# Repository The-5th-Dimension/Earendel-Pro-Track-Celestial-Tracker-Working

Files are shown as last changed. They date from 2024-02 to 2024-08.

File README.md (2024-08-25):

<h1>Earendel Pro-Track: IoT-Based Celestial Object Tracker</h1>

<h2><a href="https://github.com/linukaratnayake">Linuka Ratnayake</a>, <a href="https://github.com/YasiruDEX">Yasiru Basnayake</a>, <a href="https://github.com/KumuthuDeZoysa">Kumuthu De Zoysa</a>, <a href="https://github.com/KavinduJ2001">Kavindu Jayathissa</a>, <a href="https://github.com/ehele">Aruna Ehelepola</a>,  <a href="">Dhanushka Weerakoon</a></h2>

<h2>Overview</h2>
<h3>Introduction</h3>
<p>
    "Earendel Pro-Track" is a project that aims to design a telescope mount capable of automatically locating and keeping track of stellar objects. The desired stellar object can be selected through the user interface, and once that information is transferred to the telescope mount in the form of celestial coordinates, it turns to that stellar object, and starts observing.
</p>

<h3>Features</h3>
<ul>
    <li>No need to horizontally level the telescope mount.</li>
    <li>No need to start by pointing to the direction of North or the North Star.
    <li>Integration with online databases to obtain real-time celestial locations.</li>
    <li>Mobile app interface for easy controlling for the user.</li>
    <li>IoT communication for transmitting mount orientation data.</li>
    <li>Carefully designed for smooth and accurate celestial tracking.</li>
</ul>

https://github.com/user-attachments/assets/d0daafc0-86b6-4ca8-b112-ab7fa79acf01

To better understand the project and its problem-solution scenario, deliverables and outcomes, refer to <a href="Project Details (Documents and Media)/Project Overview Video/Earendel_Pro_Track _The_5th_Dimension.mp4">this</a> video.

<h2>Research and Development</h2>

<h3>Coordinate Systems and Conversion</h3>

| **Altitude - Azimuth** | **Right Ascension - Declination** |
|:--:|:--:|
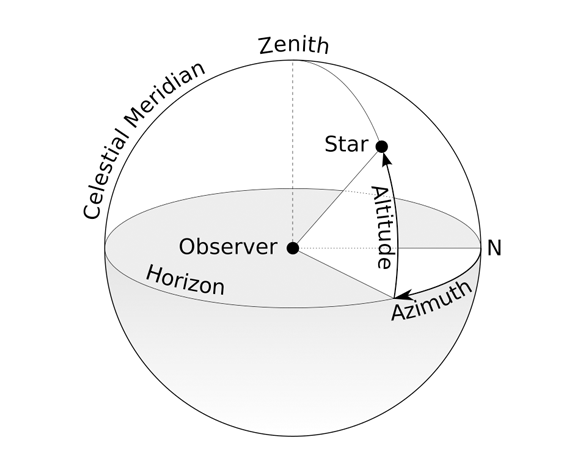
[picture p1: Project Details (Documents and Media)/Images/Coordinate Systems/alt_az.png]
ALT-AZ
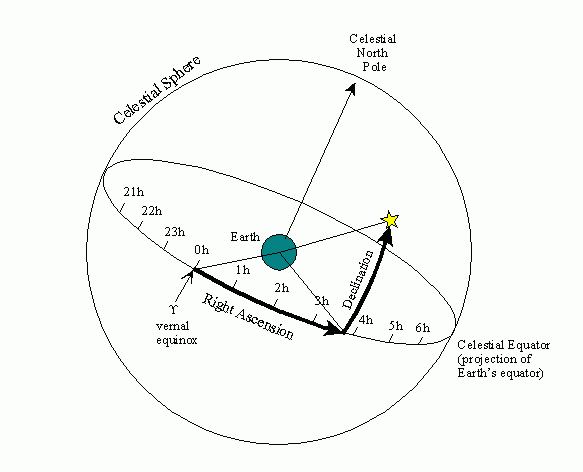
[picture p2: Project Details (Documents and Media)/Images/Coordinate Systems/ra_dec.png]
|  | |

These are two main coordinates systems used in astronomy.
Coordinates given in the latter are relatively constant and can be obtained from databases. They then need to be converted to the former, taking into consideration the user's location and the date and time.

The location and date and time are acquired from the sensors and the internet, and converted with the custom-written libraries.

<b>In this project, the conversion from Right Ascension and Declination coordinates to Altitude and Azimuth coordinates was improved by accounting for the tilt of the telescope mount. For further details, please refer to the following personal repository.

<a href="https://github.com/linukaratnayake/RADEC-to-ALTAZ-Tilted-Axes-Coordinate-Conversion">linukaratnayake/RADEC-to-ALTAZ-Tilted-Axes-Coordinate-Conversion</a></b>

**Repository Content**

<ul>
<li>Algorithm to convert Right Ascension and Declination coordinates to Altitude and Azimuth coordinates.</li>
<li>Mathematical derivation of an algorithm to compensate for the tilt in the coordinate axes.</li>
<li>Python implementation of the algorithms for testing and as a proof of concept.</li>
<li>C/C++ implementation of the algorithms to be used in the actual device.</li>
</ul>

<h2>Software Development</h2>

In the project, it was aimed to provide the flexibility to the user such that it is possible to use a mobile device or a computer to control the telescope mount. This includes developing a mobile application (currently Android, plan to extend to iOS), and a web interface, through which the user can select the desired stellar object.

Furthermore, software development includes designing of databases to store data of stars and planets, as well as handling user details.

<h3>Mobile App</h3>

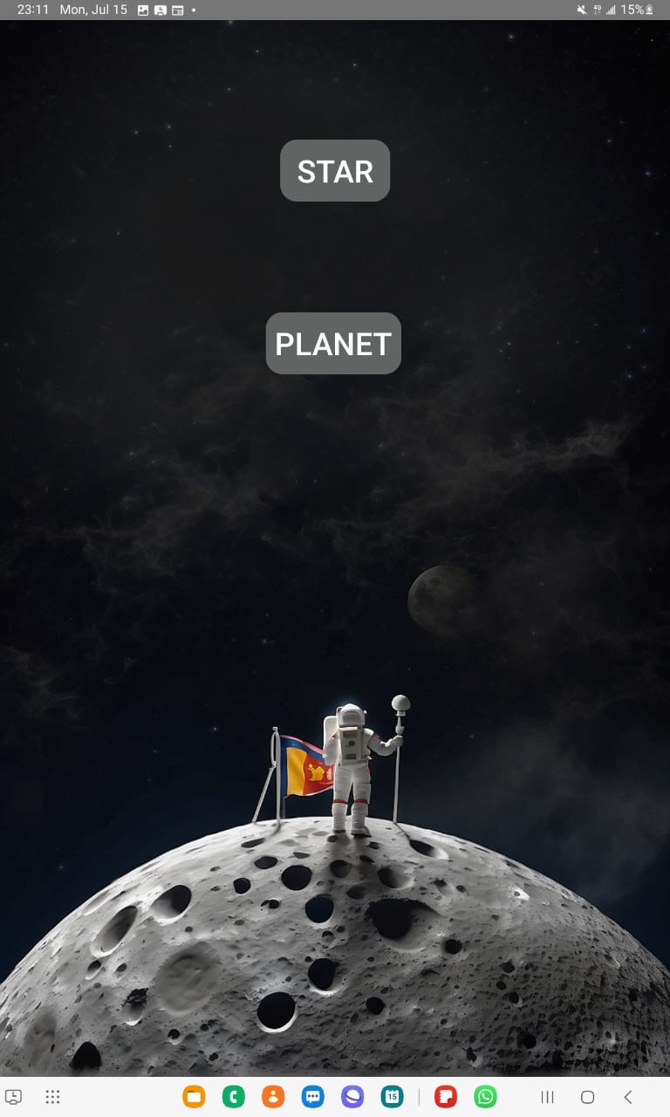
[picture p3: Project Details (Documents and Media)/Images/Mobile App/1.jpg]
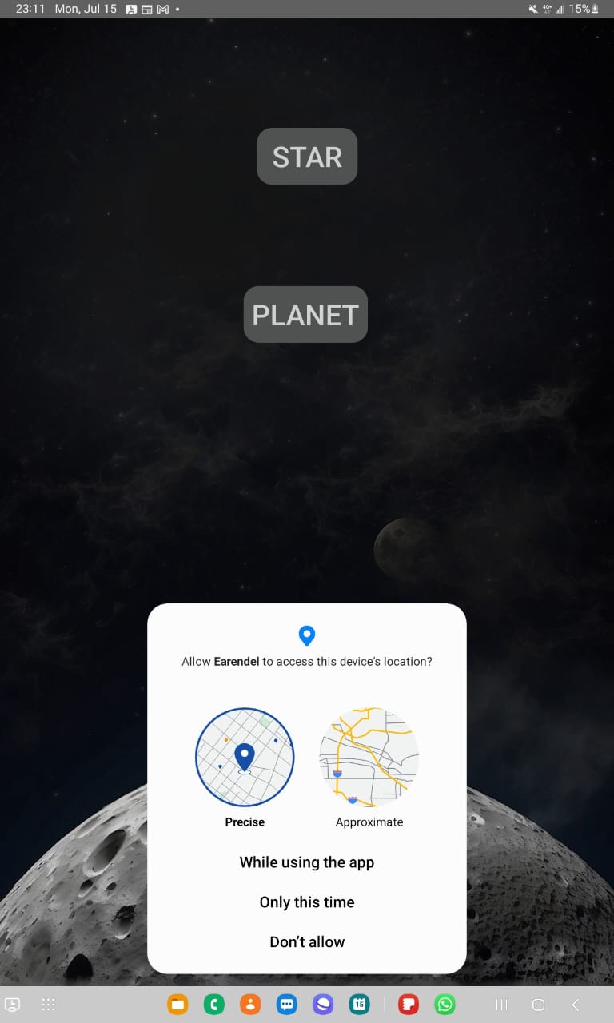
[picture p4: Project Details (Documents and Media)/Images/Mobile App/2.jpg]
|  | |
|:--:|:--:|
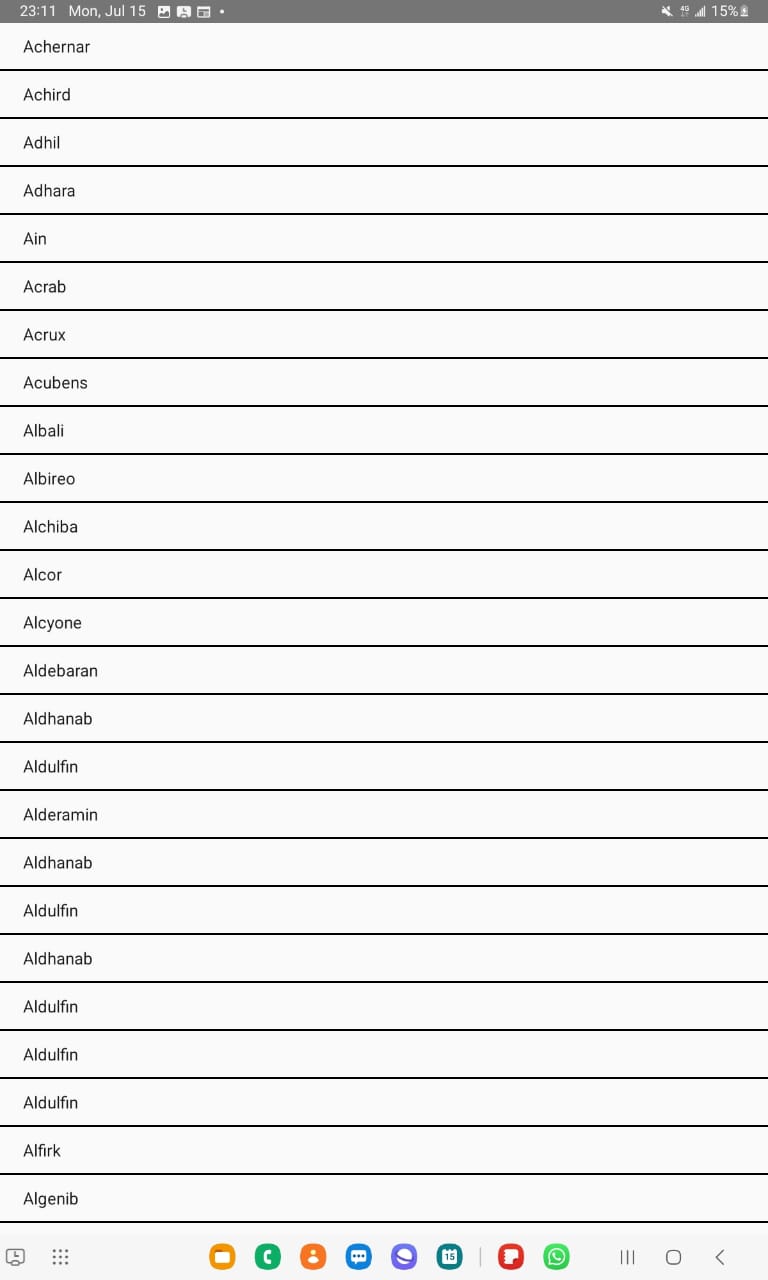
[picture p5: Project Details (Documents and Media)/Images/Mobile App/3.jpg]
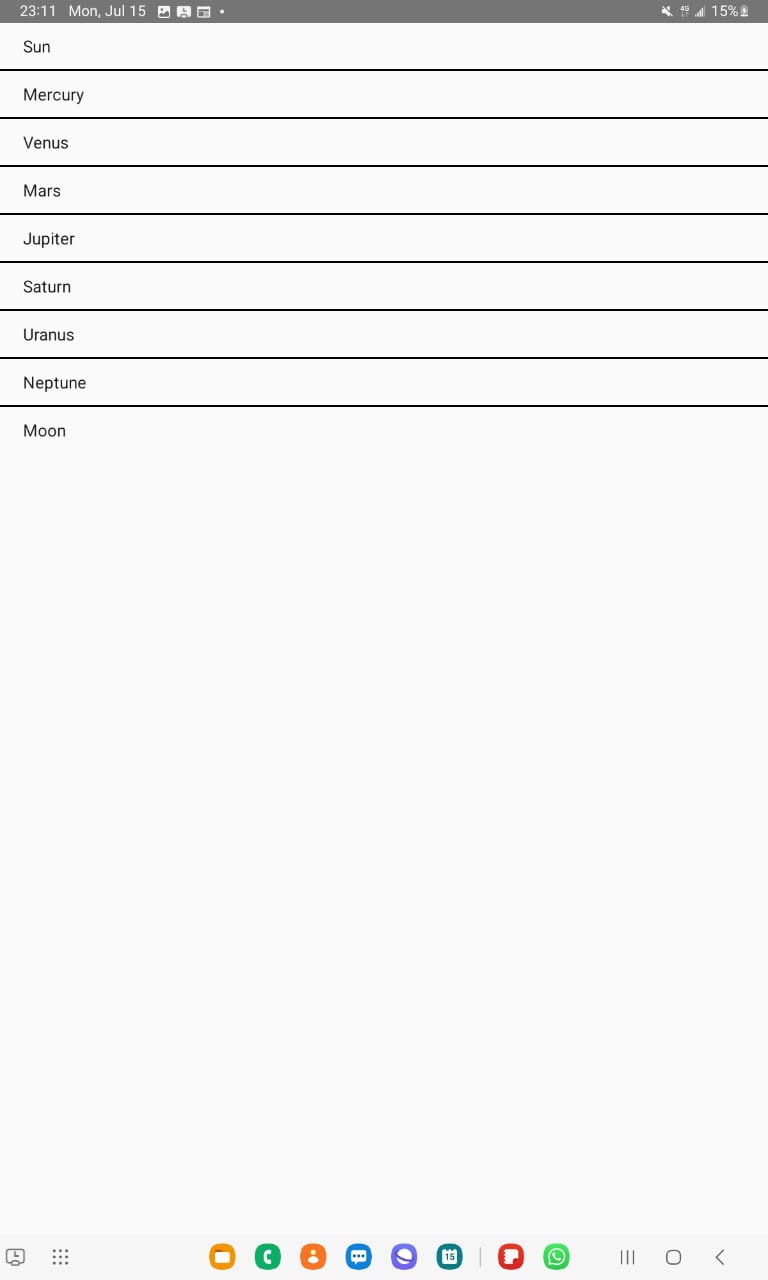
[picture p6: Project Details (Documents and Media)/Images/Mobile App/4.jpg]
|  | |

<h3>Web Application</h3>

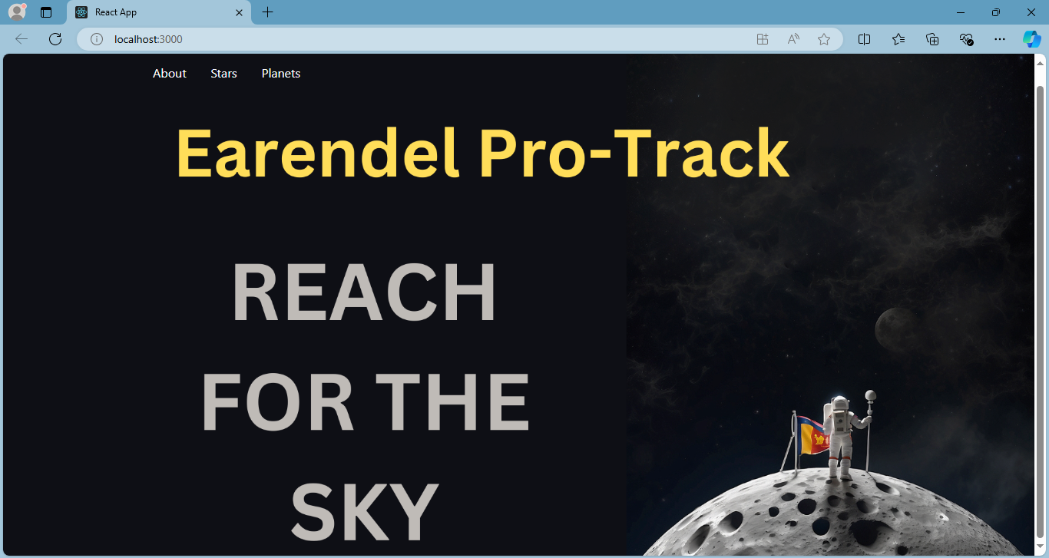
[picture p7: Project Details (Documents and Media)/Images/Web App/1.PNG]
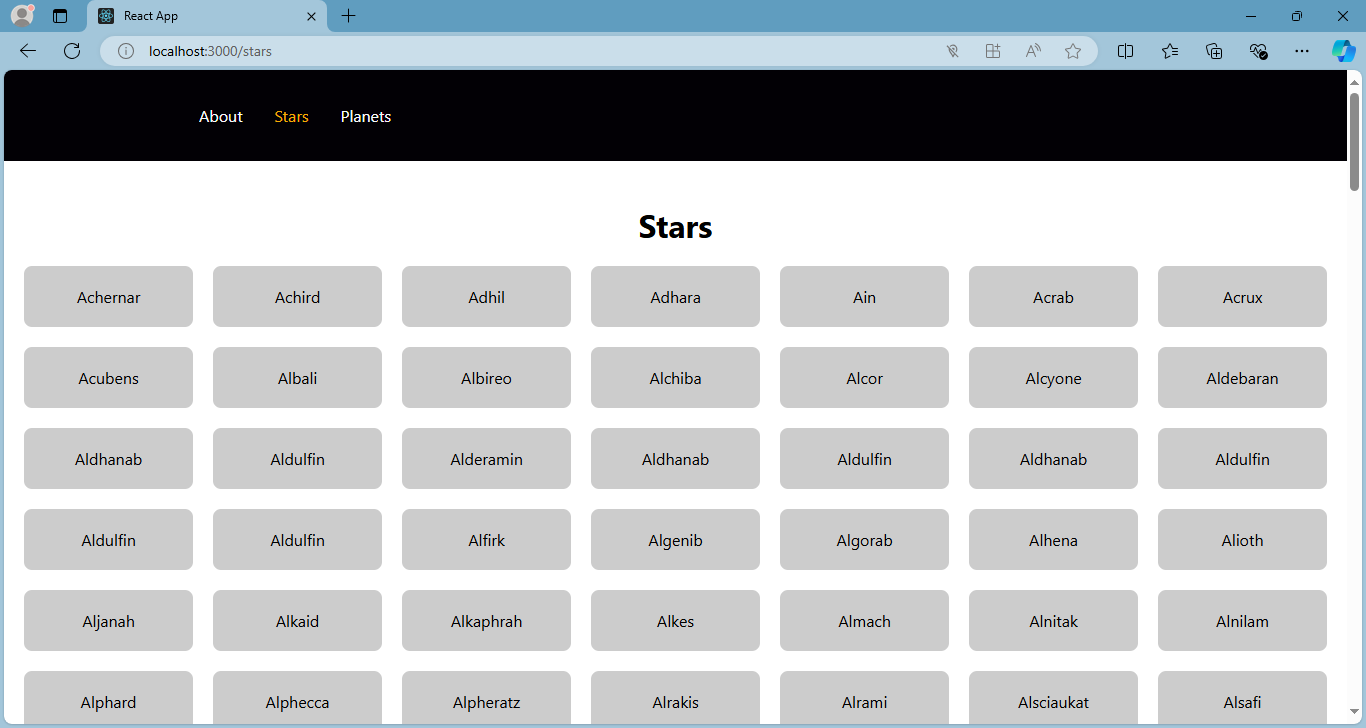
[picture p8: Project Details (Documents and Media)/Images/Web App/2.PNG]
|  | |
|:--:|:--:|
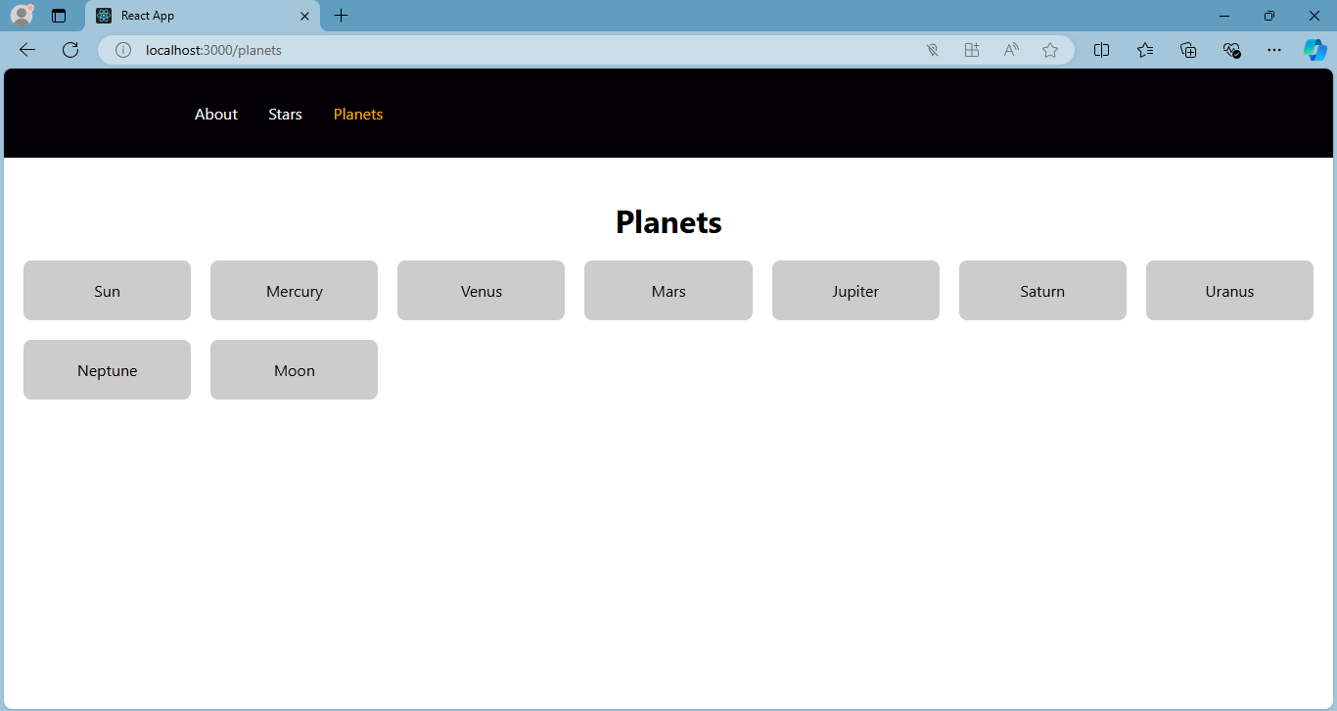
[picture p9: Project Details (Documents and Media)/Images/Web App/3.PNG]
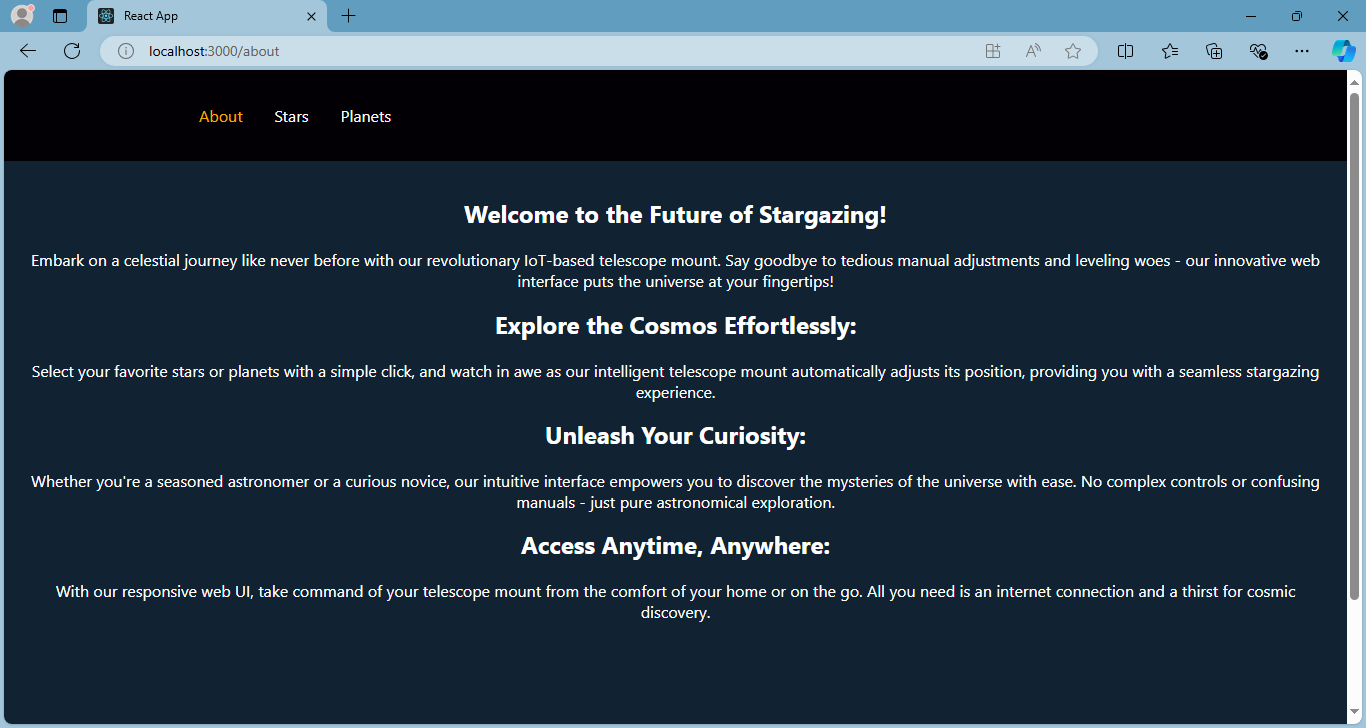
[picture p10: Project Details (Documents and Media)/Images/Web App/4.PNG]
|  | |

For codes and further details of the user application and the inclusion of databases, refer <a href="Codes/User Application/">here</a>.

<h2>PCB Design</h2>

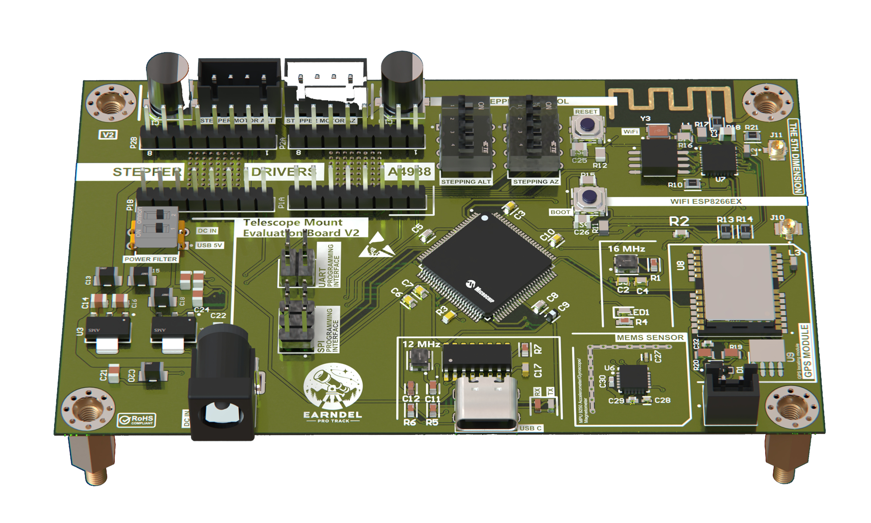
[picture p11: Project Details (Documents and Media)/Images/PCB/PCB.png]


A custom 2-layer PCB is designed using **Altium Designer**.

**Features of the PCB**
<ul>
<li>Division of synchronous and asynchronous processing parts between two microcontrollers, to reduce latency, and seamless and smoother movements.</li>
<li>2 power-up methods: DC barrel jack up to 12V, and USB type C port.</li>
<li>Compact design with on-board mounted stepper motor drivers, and control switches.</li>
<li>External connection ports for integrating accelerometer, magnetometer, and GPS module.</li>
</ul>

For PCB design files, refer <a href="PCB Design">here</a>.

<!-- <b>In the second version of the PCB, several identified issues were resolved, together with the addition of some more features. For further details, please refer to the following personal repository.

<a href="https://github.com/YasiruDEX?tab=repositories">[repo_name]</a></b> -->

<h2>Mechanical Design</h2>

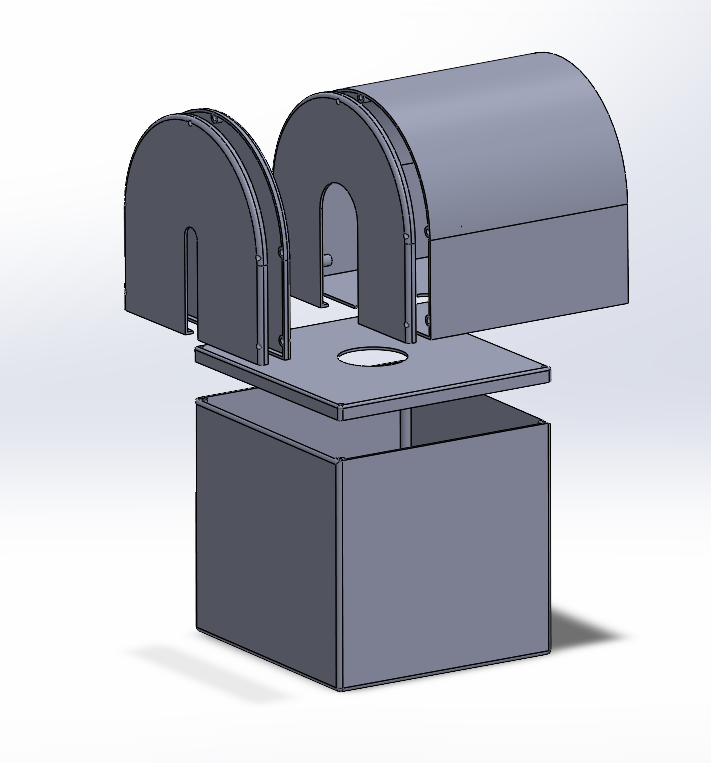
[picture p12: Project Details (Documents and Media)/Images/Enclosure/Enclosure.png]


Metal structure is designed to support the weight of the telescope, motors, and other components, with a 3D printed enclosure to enhance the visual appeal. **SOLIDWORKS** and **Blender** are used extensively for designing.

For structure and enclosure design files, and details, refer <a href="Physical Design">here</a>.

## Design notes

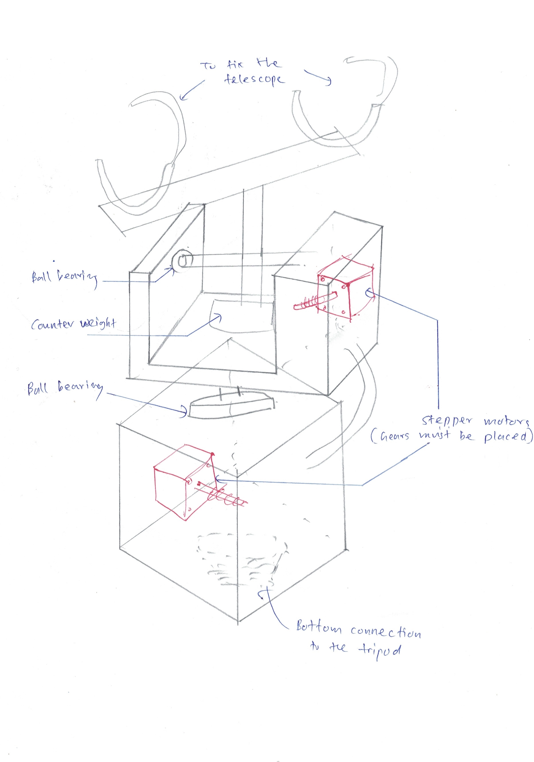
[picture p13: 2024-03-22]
Physical Design/Mount - Hand Drawn Sketches/Hand_Drawn_Sketch_1.jpg

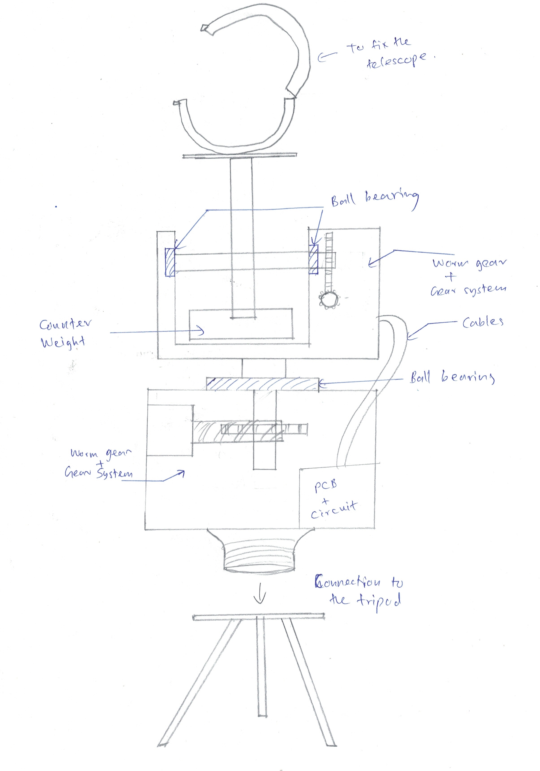
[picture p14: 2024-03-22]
Physical Design/Mount - Hand Drawn Sketches/Hand_Drawn_Sketch_2.jpg

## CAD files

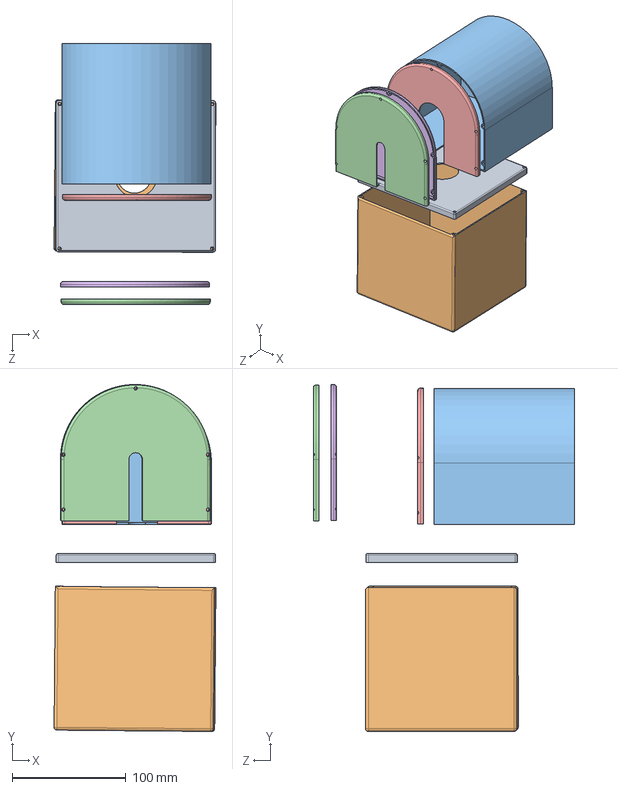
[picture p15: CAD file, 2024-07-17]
Physical Design/Enclosure Design/Assembly.SLDASM
142.2 x 304.8 x 229.7 mm
Bottom Box Lid Part
Bottom Box Part
Top Cover With Arch Part 1
Top Cover With Arch Part 2
Thin Cover Part 1
Thin Cover Part 2

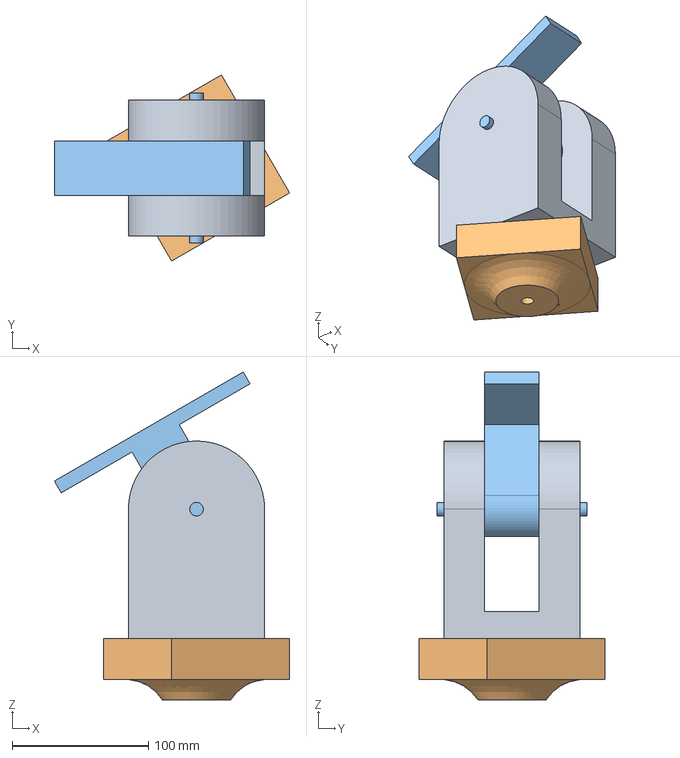
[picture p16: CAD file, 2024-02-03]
Physical Design/Mount - Initial Designs/mount.step
172.6 x 136.6 x 240.6 mm

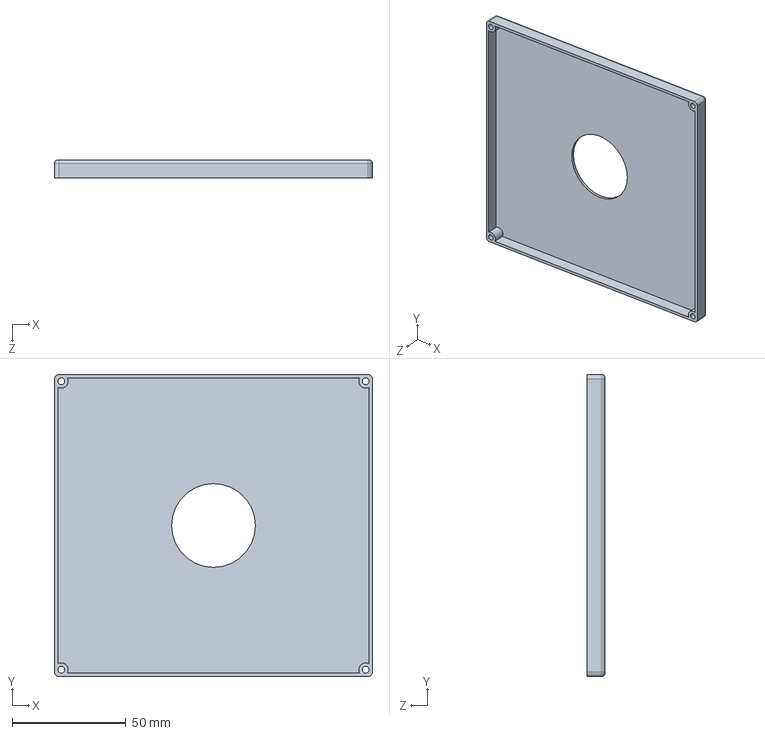
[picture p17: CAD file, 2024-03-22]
Physical Design/Enclosure Design/Bottom Box Lid Part.SLDPRT
140.0 x 133.0 x 8.00 mm

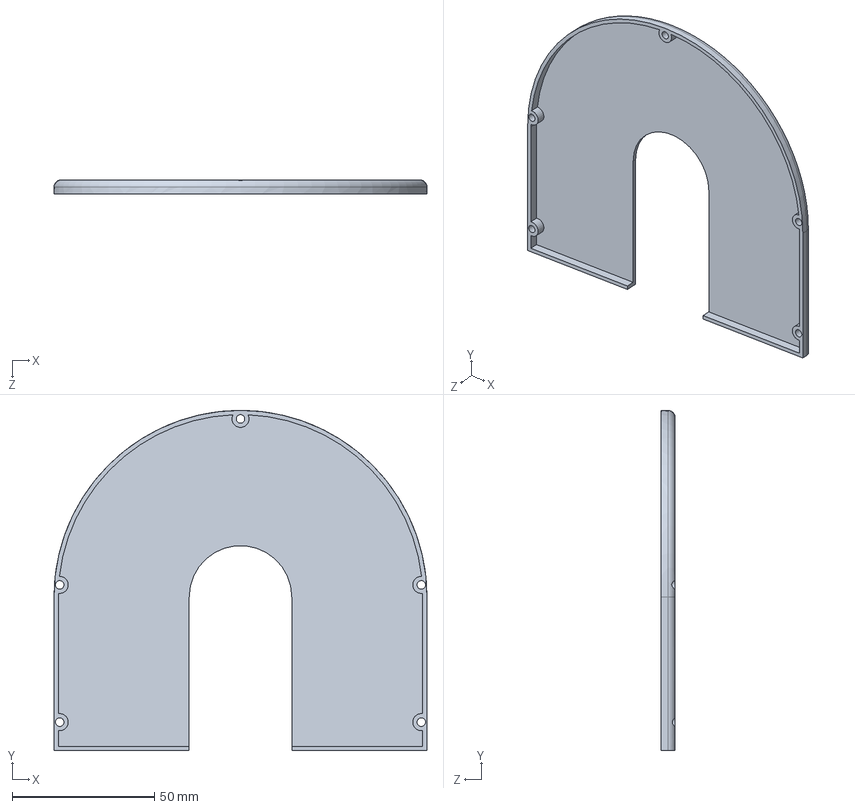
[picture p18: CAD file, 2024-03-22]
Physical Design/Enclosure Design/Thin Cover Part 1.SLDPRT
131.0 x 119.5 x 5.00 mm

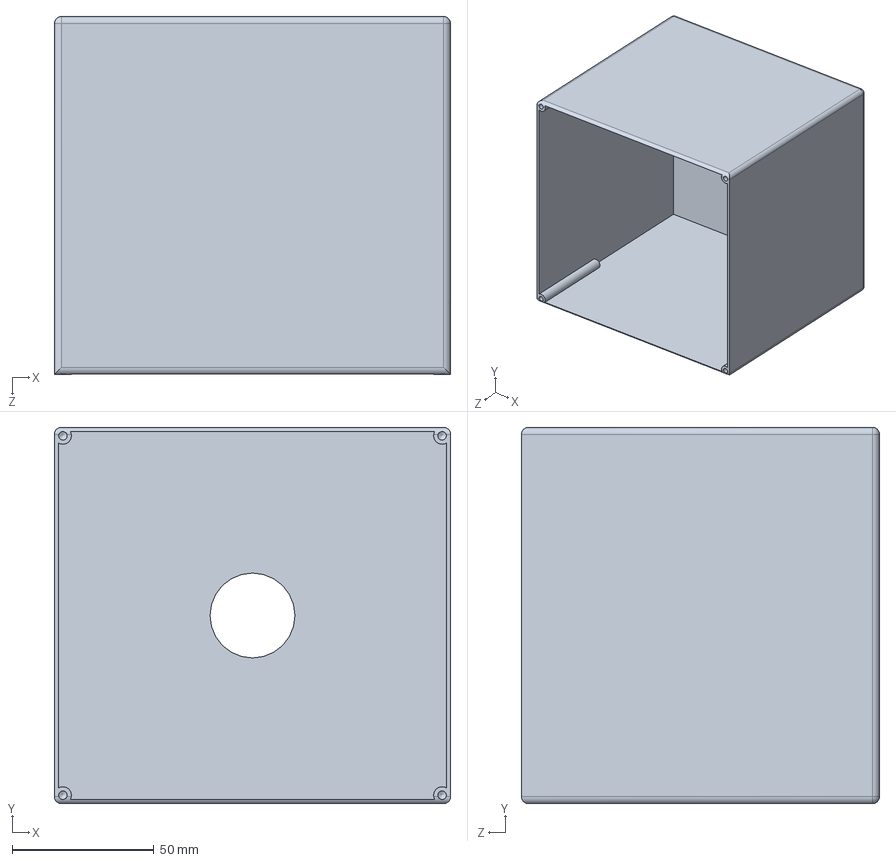
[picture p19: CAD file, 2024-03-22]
Physical Design/Enclosure Design/Bottom Box Part.SLDPRT
140.0 x 133.0 x 126.5 mm

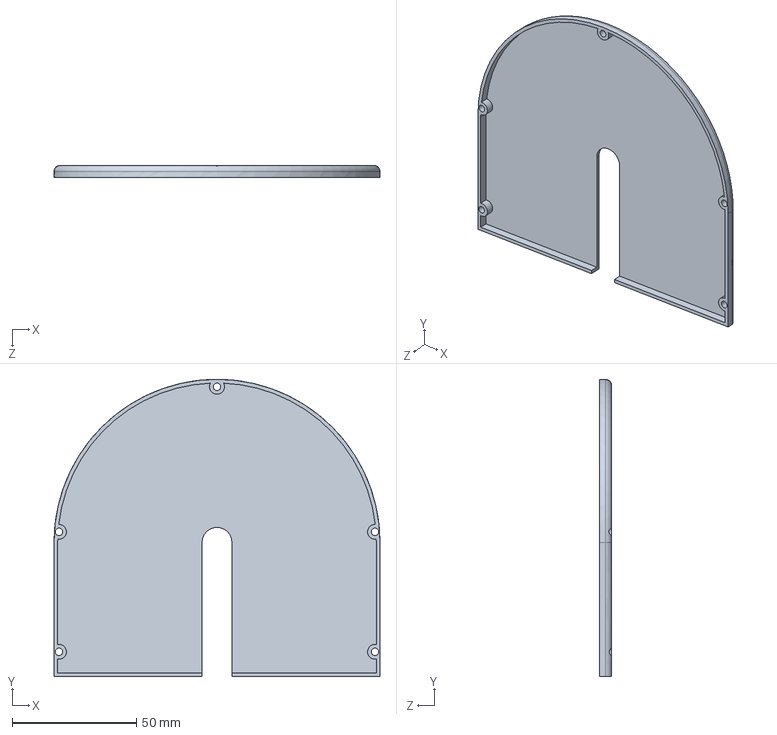
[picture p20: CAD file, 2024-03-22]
Physical Design/Enclosure Design/Top Cover With Arch Part 2.SLDPRT
131.0 x 119.5 x 5.00 mm

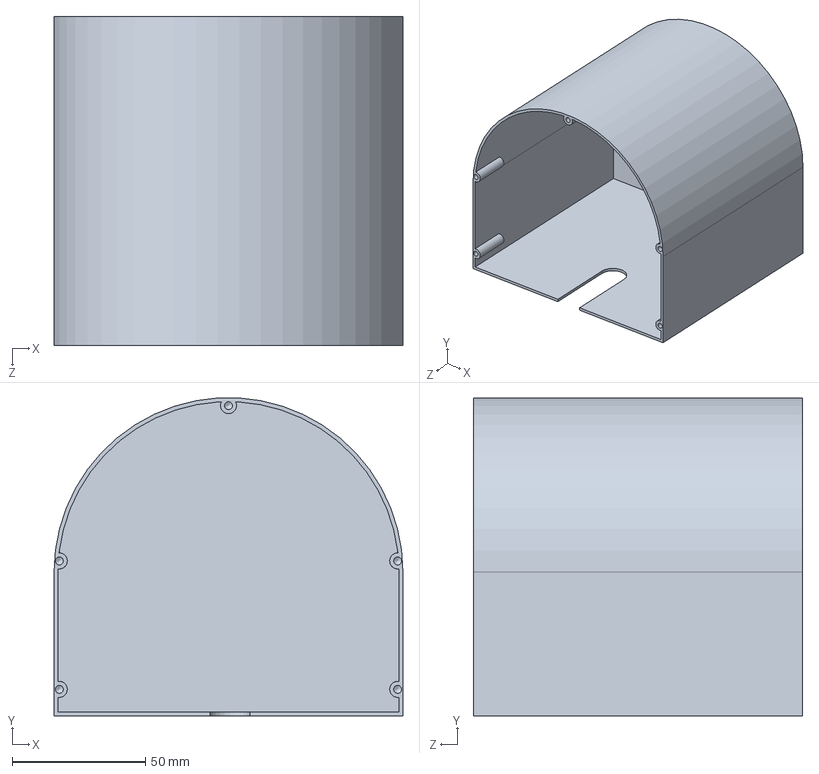
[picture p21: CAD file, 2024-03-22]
Physical Design/Enclosure Design/Top Cover With Arch Part 1.SLDPRT
131.0 x 119.4 x 123.5 mm

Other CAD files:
Physical Design/Enclosure Design/Thin Cover Part 2.SLDPRT
Physical Design/GearBox_design/V1.blend
Physical Design/GearBox_design/v2.blend
Physical Design/Mount - Initial Designs/mount.SLDPRT
Physical Design/Mount - Initial Designs/mount.dwg

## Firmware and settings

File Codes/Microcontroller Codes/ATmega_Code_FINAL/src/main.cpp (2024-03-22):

/*

PROJECT PLAN

1. Use external interrrupts to trigger a UART transfer from the ESP32.
2. Get serial data about GPS location, UTC time, and RA-DEC coordinates.
3. Use the already built library to convert RA-DEC to ALT-AZ.
4. Turn the stepper motors to the required stellar object.
5. Keep focusing until another interrupt gives another object.
(Time updates can also come from an interrupt.)

*/

#include <Arduino.h>
#include <StandardCplusplus.h>
#include <vector>
#include "CoordinateConverter.h"
#include "DataDecoder.h"
#include "Stepper.h"
#include "Accelerometer.h"
#include "PseudoMagnetometer.h"

// The accelerometer we use is an MPU6050.
#define ACC_I2C_ADDR 0x68

#define AZIMUTH_ANGULAR_RESOLUTION 5 // degrees
#define ALTITUDE_ANGULAR_RESOLUTION 5 // degrees

// #define Serial_INT 2 // Interrupts seem not working.

// Variables to be updated based on the Serial data from the ESP32.

// SOME RANDOM (EXPECTED ON DEMONSTRATION DAY) VALUES ARE SET FOR BETTER ACCURACY.
volatile int year = 2024, month = 3, day = 23, hour = 4, minute = 30; // Expected day and time of demonstration.
volatile double second = 0;
volatile double latitude = 6.9271, longitude = 79.8612;
double ra = 6.75, dec = -16.7;  // Sirius
bool valuesUpdated = true;
double currentAzimuth = 0;
unsigned int azimuthStep = 0;

// Local coordinate values.
double altitude = 0, azimuth = 0;

float roll = 0;
// float yawn = 0;

CoordinateConverter converter;
Accelerometer accelerometer;

// Function Declarations
void handleSerial();
void autoUpdateTime();
void debugPrint();
double absolute(double); // Custom function to find the absolute value.

void setup()
{
  // Serial output for debug data output.
  Serial.begin(115200);

  accelerometer.begin(ACC_I2C_ADDR);

  // Need the accelerometer to be horizontally flat.
  // If not practical, comment this out.
  // accelerometer.calibrateError();
  
  pinModeSteppers();

  // Maybe need to add some initial delay to get the initial data from the ESP32 in the setup.

  autoUpdateTime(); 
}

void loop()
{
  handleSerial();

  if (valuesUpdated)
  {
    converter.updateLocation(latitude, longitude);
    converter.updateDateUTC(day, month, year);
    converter.updateTimeUTC(hour, minute, second);
    converter.update_RA_DEC(ra, dec);
    valuesUpdated = false;
  }

  converter.updateTimeUTC(hour, minute, second);
  converter.updateDateUTC(day, month, year); // Only necessary on a moment after midnight.

  vector<double> altaz = converter.convert();
  altitude = altaz[0];
  azimuth = altaz[1];

  // Lowest angle for the telescope is 0 degrees.
  if (altitude < 0) {
    altitude = 0;
  }

  // Turn bottom part to `azimuth`.

  // ===== WORKS ONLY WITH A MAGNETOMETER =====
  // yawn = 0; // Magnetometer.getYawn();  // This should return absolute angle from the North.
  // bool motorDirectionDown = (azimuth - yawn) >= 0;  // Might neeed to change to <=, depending on the actual setup.
  // if (absolute(azimuth - yawn) > AZIMUTH_ANGULAR_RESOLUTION) {
  //   rotate(STEPPER_DOWN, motorDirectionDown);
  // }
  // ==========


  // ALTERNATE METHOD WITHOUT A MAGNETOMETER
  // THIS METHOD REQUIRES THE INITIAL ALIGNMENT TO NORTH.
  //========================
  bool motorDirectionDown;
  // Might need to interchange >= and <, depending on the actual setup.
  if (currentAzimuth >= azimuth) {
    motorDirectionDown = DIR_1;
  }
  else if (currentAzimuth < azimuth) {
    motorDirectionDown = DIR_2;
  }

  double remainingAngle = absolute(currentAzimuth - azimuth);


  if ((azimuthStep < angleToSteps(remainingAngle)) &&  (absolute(currentAzimuth - azimuth) > AZIMUTH_ANGULAR_RESOLUTION)) {
    rotate(STEPPER_DOWN, motorDirectionDown);
    if (currentAzimuth >= azimuth) {
      currentAzimuth -= stepsToAngle(1);
    }
    else if (currentAzimuth < azimuth) {
      currentAzimuth += stepsToAngle(1);
    }
    azimuthStep++;
  }

  // Turn top part to `altitude`.
  roll = accelerometer.getRoll(); // Either roll or pitch depending on how the accelerometer is mounted.
  bool motorDirectionUp = altitude >= roll;  // Might neeed to change to <=, depending on the actual setup.
  if (absolute(altitude - roll) > ALTITUDE_ANGULAR_RESOLUTION) {
    rotate(STEPPER_UP, motorDirectionUp);
  }

  // // DEBUG
  // debugPrint();
}

// Function Definitions
void handleSerial()
{
  if (Serial.available())
  {
    const int buffSize = 50;
    char input[buffSize];
    Serial.readStringUntil('\n').toCharArray(input, buffSize);

    data inputData = decode(input);

    if (inputData.type == "DATE")
    {
      day = (int)inputData.value1;
      month = (int)inputData.value2;
      year = (int)inputData.value3;
    }
    else if (inputData.type == "TIME")
    {
      hour = (int)inputData.value1;
      minute = (int)inputData.value2;
      second = inputData.value3;
    }
    else if (inputData.type == "GPS")
    {
      latitude = inputData.value1;
      longitude = inputData.value2;
    }
    else if (inputData.type == "RADEC")
    {
      ra = inputData.value1;
      dec = inputData.value2;
    }

    valuesUpdated = true;
  }

  // == TODO ==
  // Send an acknowledgement back to the ESP32 after a successful reception of data.
}

void autoUpdateTime()
{
  // The following are internal registers in ATmega328.
  // Internal interrupts (Timers) are used to keep track of time precisely.
  TCCR1A = 0;
  TCCR1B = 0;
  TCNT1 = 3036;
  TCCR1B |= (1 << CS12);
  TIMSK1 |= (1 << TOIE1);
}

ISR(TIMER1_OVF_vect)
{
  second += 1;
  if (second >= 60)
  {
    second = 0;
    minute += 1;
  }
  if (minute >= 60)
  {
    minute = 0;
    hour += 1;
  }
  if (hour >= 24)
  {
    hour = 0;
    day += 1;
  }
  // This should be extended to work well with month and year boundaries.
  // e.g.: Update from 30th June to 1st of July.
  // However, let's assume this is enough for demonstration.

  // Setting back to 3036, otherwise it starts back from 0.
  TCNT1 = 3036;
}

void debugPrint() {
  Serial.print(String(year) + "." + String(month) + "." + String(day) + "\t");
  Serial.print(String(hour) + ":" + String(minute) + "." + String(second) + "\t");
  Serial.print("Latitude: " + String(latitude) + ", Longitude: " + String(longitude) + "\t");
  Serial.print("RA: " + String(ra) + ", DEC: " + String(dec) + "\t");
  Serial.print("Altitude: " + String(altitude) + ", Azimuth: " + String(azimuth) + "\t");
  // Serial.print("Roll: " + String(roll) + ", Yawn: " + String(yawn) + "\t");
  Serial.print("Roll: " + String(roll) + ", CurrentAzimuth: " + String(currentAzimuth) + "\t");
  Serial.println();
}

double absolute(double value) {
  if (value >=0 ) {
    return value;
  }
  else {
    return -1 * value;
  }
}

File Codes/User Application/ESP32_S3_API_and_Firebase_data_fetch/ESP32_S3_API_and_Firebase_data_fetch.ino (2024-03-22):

#include <Arduino.h>
#include "WiFiManager.h"
#include "FirebaseManager.h"
#include "HTTPManager.h"
#include "LCDManager.h"
#include <time.h>

LiquidCrystal_I2C lcd(0x27, 20, 4);

#define _SSID "Dialog 4G 752"         // Your WiFi SSID
#define _PASSWORD "b10F79cD"     // Your WiFi Password
// #define _SSID "Yasiru's Galaxy Tab"          // Your WiFi SSID
// #define _PASSWORD "unlimited"      // Your WiFi PasswordString serverPath = serverName;
const char* referenceUrl = "earendeldata-default-rtdb.asia-southeast1.firebasedatabase.app";
const char* httpUrl = "https://api.visibleplanets.dev/v3?latitude=7.4818&longitude=80.3609&showCoords=true&aboveHorizon=false";
const char* FirebaseUrl = "https://earendeldata-default-rtdb.asia-southeast1.firebasedatabase.app/";

const char* ntpServer = "pool.ntp.org";
const long  gmtOffset_sec = 0; // Timezone offset in seconds (e.g. 0 for GMT)
const int   daylightOffset_sec = 3600; // Daylight offset in seconds (e.g. 3600 for DST)

#define az "Z"
#define alt "Y"

FirebaseManager firebase(referenceUrl);
WiFiManager wifiManager(_SSID, _PASSWORD, lcd);
HTTPManager httpManager;
// FirebaseManagerNew httpManager;

const int MAX_PLANETS = 10;
const int numberOfPlanets = 10;

float az_current_angle = 0;
float alt_current_angle = 0;
float az_to_turn = 0;
float alt_to_turn = 0;

String planetNames[MAX_PLANETS];
String raValues[MAX_PLANETS];
String decValues[MAX_PLANETS];

const String planetsWithMoon[numberOfPlanets] = {
  "Sun", "Moon", "Mercury", "Venus", "Mars", "Jupiter", "Saturn", "Uranus", "Neptune"
};

String planetNeeded;
String starData;
String prevPlanet;

int now_time;

// Function declarations
int findIndex(const String array[], int size, const String &targetValue);
void initialize();
void handlePlanetData();
void handleStarData();

void setup() {
  lcd.init();
  lcd.backlight();
  Serial.begin(115200);
  // pinMode(LED_BUILTIN, OUTPUT);
  // digitalWrite(LED_BUILTIN, LOW);
  WiFi.mode(WIFI_STA);
  WiFi.disconnect();
  delay(1000);

  // Connect to WiFi
  Serial.println();
  Serial.println();
  Serial.print("Connecting to: ");
  Serial.println(_SSID);
  WiFi.begin(_SSID, _PASSWORD);

  while (WiFi.status() != WL_CONNECTED) {
    delay(500);
    Serial.print("-");
  }

  Serial.println("");
  Serial.println("WiFi Connected");

  // Print the IP address
  Serial.print("IP Address: ");
  Serial.print("http://");
  Serial.print(WiFi.localIP());
  Serial.println("/");
  // digitalWrite(LED_BUILTIN, HIGH);

//================================================================//
//================================================================//


  Serial.println();
  Serial.println();
  Serial.println();
  // initialize();
  now_time = -30;

  // Initialize and synchronize the time
  configTime(gmtOffset_sec, daylightOffset_sec, ntpServer);

  // Wait for time to be set
  while (!time(nullptr)) {
    delay(1000);
    Serial.println("Waiting for time to sync...");
  }

}

void loop() {

  // Get current time
  time_t now;
  struct tm timeinfo;
  char strftime_buf[64];

  time(&now);
  localtime_r(&now, &timeinfo);
  
  // Format time into a string
  strftime(strftime_buf, sizeof(strftime_buf), "%Y-%m-%d %H:%M:%S", &timeinfo);
  
  // Print time to serial
  Serial.print("Current time: ");
  Serial.println(strftime_buf);

  if (millis()/1000 - now_time >= 10){
    planetNeeded = firebase.getString("Planet");
    // planetNeeded = "Sun";

    Serial.println(planetNeeded);
    
    bool planetFound = findIndex(planetsWithMoon, numberOfPlanets, planetNeeded) != -1;
    
    if (planetFound) {
      handlePlanetData();
    } else {
      handleStarData();
    }

    prevPlanet = planetNeeded;
    Serial.println();
    now_time = millis()/1000;
  }

    if(int(az_to_turn) != int(az_current_angle)){
      if (az_to_turn > az_current_angle){
      Step(az, 1, true);
      az_current_angle += 1.8;
      // delay(50);
      }else if (az_to_turn < az_current_angle){
      Step(az, 1, false);
      az_current_angle -= 1.8;
      // delay(50);
      }
    }

    if(int(alt_to_turn) != int(alt_current_angle)){
      if (alt_to_turn > alt_current_angle){
      Step(alt, 1, true);
      alt_current_angle += 1.8;
      // delay(50);
      }else if (alt_to_turn < alt_current_angle){
      Step(alt, 1, false);
      alt_current_angle -= 1.8;
      // delay(50);
      }
    }

    // zAxisServo.write(az_current_angle);
    // Serial.print(alt_to_turn);
    // Serial.print(" : ");
    // Serial.print(alt_current_angle);
    // Serial.print(" : ");
    // Serial.print(az_to_turn);
    // Serial.print(" : ");
    // Serial.println(az_current_angle);
}

// Function definitions
void initialize() {
  wifiManager.connect();
}

void handlePlanetData() {
  Serial.print("Finding Planet Data");
  httpManager.fetchData(httpUrl, planetNames, raValues, decValues);

  int index = findIndex(planetNames, MAX_PLANETS, planetNeeded);

  if (index != -1) {
    int degreeIndex = raValues[index].indexOf('h');
    int altdegreeIndex = decValues[index].indexOf("°");
    Serial.print(decValues[index]);
    Serial.println(planetNeeded + " : RA: " + raValues[index] + " : DEC:" + decValues[index]);

    az_to_turn = int(atoi(raValues[index].substring(0, degreeIndex).c_str())/1.8) * 7 * 1.8 * 2;

    alt_to_turn = -abs(int(atoi(decValues[index].substring(0, altdegreeIndex).c_str())/1.8))  * 1.8;

    if(az_to_turn >= 360){az_to_turn -= 360;}

    lcd.setCursor(0, 1);
    lcd.print("              ");
    lcd.setCursor(0, 1);
    lcd.print(planetNeeded + ":");
    lcd.setCursor(0, 2);
    lcd.print("RA: " + String(raValues[index]));
    lcd.setCursor(0, 3);
    lcd.print("DEC: " + String(decValues[index]));
  } else {
    Serial.println("Planet not found!");
  }
}

void handleStarData() {
  if (planetNeeded != prevPlanet) {
    starData = firebase.getString(planetNeeded);
  }

  az_to_turn = int(atoi(starData.substring(3, 10).c_str())/1.8) * 7 * 1.8 * 2;

  alt_to_turn = -abs(int(atoi(starData.substring(15, 24).c_str())/1.8))  * 1.8;

  if(az_to_turn >= 360){az_to_turn -= 360;}


  Serial.println(planetNeeded + ": " + starData);
  lcd.setCursor(0, 1);
  lcd.print("              ");
  lcd.setCursor(0, 1);
  lcd.print(planetNeeded + ":");
  lcd.setCursor(0, 2);
  lcd.print(starData.substring(0, 10));
  lcd.setCursor(0, 3);
  lcd.print(starData.substring(11, 24));
}

int findIndex(const String array[], int size, const String &targetValue) {
  for (int i = 0; i < size; i++) {
    if (array[i] == targetValue) {
      return i;
    }
  }
  return -1;
}
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

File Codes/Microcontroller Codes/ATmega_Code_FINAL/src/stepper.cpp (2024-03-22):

#include <Arduino.h>
#include "Stepper.h"

void pinModeSteppers() {
    pinMode(STEPPER_DOWN_STEP, OUTPUT);
    pinMode(STEPPER_DOWN_DIR, OUTPUT);

    pinMode(STEPPER_UP_STEP, OUTPUT);
    pinMode(STEPPER_UP_DIR, OUTPUT);
}

void rotate(int motor, int direction) {
    if (motor == STEPPER_DOWN) {
        if (direction == DIR_1) {
            digitalWrite(STEPPER_DOWN_DIR, LOW);
        }
        else if (direction == DIR_2) {
            digitalWrite(STEPPER_DOWN_DIR, HIGH);
        }

        digitalWrite(STEPPER_DOWN_STEP, HIGH); 
        delayMicroseconds(500);
        // delay(30);
        digitalWrite(STEPPER_DOWN_STEP, LOW); 
        delayMicroseconds(500);
        // delay(30);
    } else if (motor == STEPPER_UP) {
        if (direction == DIR_1) {
            digitalWrite(STEPPER_UP_DIR, LOW);
        }
        else if (direction == DIR_2) {
            digitalWrite(STEPPER_UP_DIR, HIGH);
        }

        digitalWrite(STEPPER_UP_STEP, HIGH); 
        delayMicroseconds(500);
        // delay(30);
        digitalWrite(STEPPER_UP_STEP, LOW); 
        delayMicroseconds(500);
        // delay(30);
    }
}

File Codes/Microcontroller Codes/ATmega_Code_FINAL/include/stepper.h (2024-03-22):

#ifndef STEPPER_H
#define STEPPER_H

#define STEPPER_DOWN 0
#define STEPPER_UP 1

#define DIR_1 0
#define DIR_2 1

#define STEPPER_DOWN_STEP 5
#define STEPPER_DOWN_DIR 7

#define STEPPER_UP_STEP 6
#define STEPPER_UP_DIR 8


void pinModeSteppers();
void rotate(int, int);

#endif

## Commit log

2024-01-10 Update: gyro visualization
2024-01-10 Update:: Firebase and real time data
    issue: GET fails after reading data from firebase
    [Firebase_data_fetch_with_real_time_planet_Locations.ino, Firebase_with_latest_libraries.ino]
2024-01-10 HTTP clash resolves
    issue: Only one fetch after first fetch
    [Firebase_data_fetch_with_real_time_planet_Locations.ino]
2024-01-11 update: OOM issue solved
    Vector memory allocation had some memory leaks
    [Firebase_data_fetch_with_real_time_planet_Locations.ino]
2024-01-12 update: Planet filter
2024-01-12 update: PID roll, Z- axis
2024-01-25 Update API_and_Firebase_data_fetch_with_actuators.ino
    Stepper integration
2024-01-25 Add physical design files
    [mount.SLDPRT, mount.dwg, mount.step]
2024-01-30 Test coordinate conversion in Arduino
    Test coordinate conversion in a real Arduino board.
    Modify an Arduino library for C++ STL (Standard Template Library) to work properly.
2024-01-31 Update: Stepper motor step count calculation
2024-02-10 update: Mechanical Gear system sketching
2024-02-16 Update the app to track user location
2024-02-19 update: 3d files
    [FINAL ASS - disque-2.STL, FINAL ASS - idee-1 8-1.STL, FINAL ASS - idee-1 8-2.STL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]
2024-02-23 update: Cleaned 3D sketch files
    [FINAL ASS - disque-2.STL, FINAL ASS - idee-1 8-1.STL, FINAL ASS - idee-1 8-2.STL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]
2024-02-24 update: Biassing the Atmega
    [Earendel_PCB_design.PrjPcb, main.SchDoc]
2024-02-24 update: PCB design
    [Earendel_PCB_design.PrjPcb, PCBmain.PcbDoc, asynchronous.SchDoc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]
2024-02-24 update: Top layer
    [PCBmain.PcbDoc, Top_domain.SchDoc, synchronous.SchDoc]
2024-02-24 Add hand-drawn sketches
    Add hand-drawn sketches of the final physical realization of the telescope mount.
2024-02-24 update: PCB design power ports and GPS pins
    [Earendel_PCB_design.PrjPcb, PCBmain.PcbDoc, Power.SchDoc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]
2024-02-24 update: Depth into hierarchical design
    [PCBmain.PcbDoc, Power.SchDoc, Top_domain.SchDoc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]
2024-02-25 update: PCB design sensor interfacing, power regulation
    [Power.SchDoc, Sensor_interfacing.SchDoc, Top_domain.SchDoc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]
2024-02-25 update: Stepper control
    [Earendel_PCB_design.SCHLIB, PCBmain.PcbDoc, Power.SchDoc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]
2024-02-25 update: Clarity
    [Earendel_PCB_design.PrjPcb, PCBmain.PcbDoc, Power.SchDoc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]
2024-02-25 update: Component alligning
    [Earendel_PCB_design.PrjPcb, Power.SchDoc, Sensor_interfacing.SchDoc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]
2024-02-25 update: board size reduction and reorganizing
    [Power.SchDoc]
2024-02-25 update: Voltage regulators correctly biassed
    ESP baissing boot and reset missing
2024-02-25 update: Esp boot and reset issues fixed
    [asynchronous.SchDoc]
2024-02-25 update: Tracing
    [Stepper_control.SchDoc, synchronous.SchDoc]
2024-02-26 update: Transfer for non constraint management
    [Earendel_PCB_design.PrjPcb, Earendel_Rules_Enabled_V2.PrjPcb, Power.SchDoc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]
2024-02-26 update: asynchronious sch
    [Earendel_Rules_Enabled_V2.PrjPcb, Top_domain.SchDoc, asynchronous.SchDoc]
2024-02-27 update: ESP 32 partial convertion
    [Earendel_Rules_Enabled_V2.PrjPcb, Power.SchDoc, Stepper_control.SchDoc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]
2024-02-28 update: PCB finalized
    [Top_domain.SchDoc, asynchronous.SchDoc, synchronous.SchDoc]
2024-02-29 Add (partially) interrupt to read Serial data
2024-02-29 Add StandardCplusplus library to use C++ STL in Arduino
2024-02-29 Add timer interrupts to update local time
2024-02-29 update: STM32 HTTP compatibility : Partial
2024-03-01 Add ESP32 data decoding part
2024-03-01 update: PCB final files
2024-03-02 update: PCB outputs
    [Earendel_Rules_Enabled_V2.PrjPcb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]
2024-03-18 Add code related to controlling stepper motors
2024-03-18 Test Serial input from an actual device
    Previously, tested with user inputs through Serial Monitor.
    Now tested with ESP32.
    Interrupts not working.
    [Serial_Input_Test.ino, Serial_Output_Test.ino]
2024-03-19 Add code related to Accelerometer (MPU6050)
2024-03-19 Test Roll and Pitch from the Accelerometer
2024-03-19 Change Accelerometer library
2024-03-21 update: NTP server and ESP32 compatible HTTPManager Library updated
    [v2.blend]
2024-03-21 Add basics of motor control to main code
2024-03-21 Add code to print variable values (DEBUG)
2024-03-22 Create Enclosure Design
    [Bottom Box Lid Part.SLDPRT, Bottom Box Part.SLDPRT, Thin Cover Part 1.SLDPRT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]
2024-03-22 Configure project for both Arduino Uno and Arduino Mega
2024-03-22 Add alternate code to mimic magnetometer behavior
2024-03-22 Develop the web application for Earendel Pro Track
2024-07-11 Update folder structure
    [Earendel_PCB_design.PrjPcb, Earendel_PCB_design.SCHLIB, Earendel_Rules_Enabled_V2.PrjPcb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]
2024-07-16 Add enclosure assembly file and update readme
    [Assembly.SLDASM]
2024-07-26 Update README.md
    Resolve issue with embedded video.
    Resize PCB image to better see details.
